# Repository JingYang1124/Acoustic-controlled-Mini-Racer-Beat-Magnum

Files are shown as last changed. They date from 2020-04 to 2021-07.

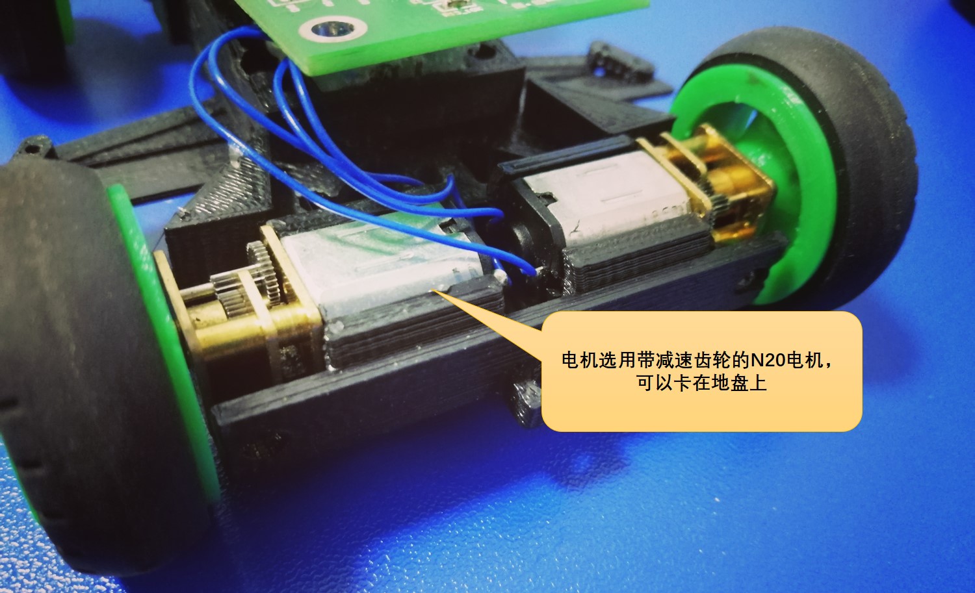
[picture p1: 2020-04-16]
Image/2_电机固定.jpg

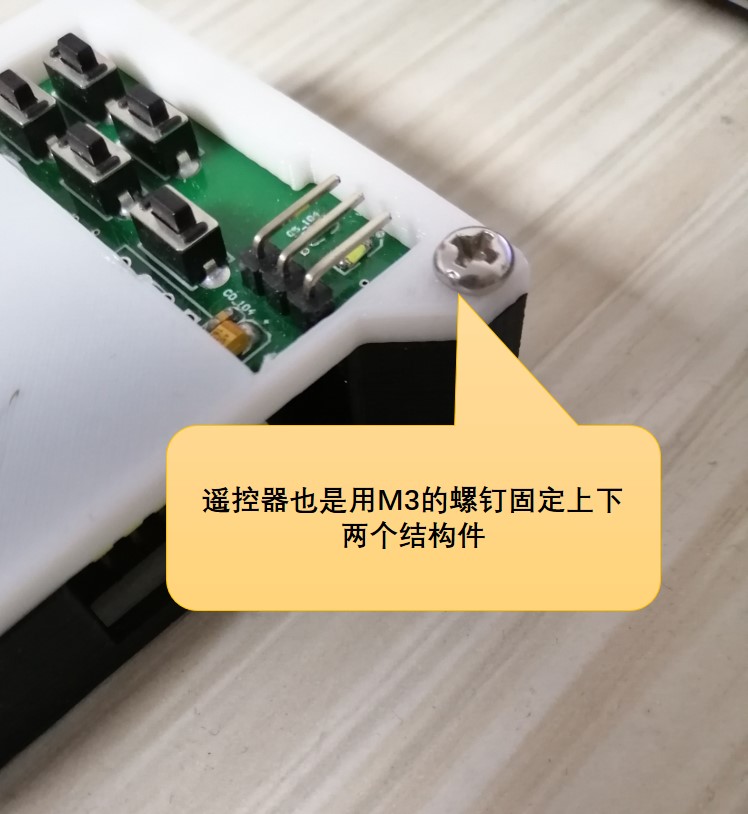
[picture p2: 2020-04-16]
Image/6_遥控器固定.jpg

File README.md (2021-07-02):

# 声控的迷你赛车--“跃动冲锋”
  

本项目是一款声控的迷你赛车--“跃动冲锋”，可通过语音指令控制车子的运动，还原了动画片“四驱兄弟”中的场景。

项目演示视频：

> [【自制】声控版! 前进，跃动冲锋！_哔哩哔哩_bilibili](https://www.bilibili.com/video/BV11g4y1879b)

1_声控版“跃动冲锋”

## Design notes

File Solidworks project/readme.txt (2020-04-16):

Solidworks版本：Solidworks 18   
Car_base文件夹中工程为车子底盘的模型
Transmitter文件夹中工程为遥控器的模型

上述文件夹内包括了装配体模型以及每一个小部件的模型

如果您的Solidworks版本低打不开上述模型，或者没有您安装solidworks，也可以直接使用stl文件进行3D打印
底盘打印时，可以直接打印：
mark3.STL                （1个）
back_lock.STL          （1个）
back_wheel.STL       （2个）
Racer_Lock.STL        （1个）
board_support.STL  （1个）
frontwheellock.STL  （2个）

遥控器打印时，可以直接打印：
Transmitter_base.STL    （1个）
Trans_part2.STL            （1个）

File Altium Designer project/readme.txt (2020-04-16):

Altium Designer版本：Altium Designer 18   
Beat_magnum_transmitter 文件夹中工程为语音遥控器的PCB
Beat_magnum_receiver 文件夹中工程为车子上的PCB

文件夹内包含了PCB导出的Gerber文件，可以直接将其发送给PCB厂家生产

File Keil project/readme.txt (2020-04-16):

Keil版本： Keil 5
Beat_magnum_transmitter 为语音遥控器上的程序
Beat_magnum_receiver 为车子上的程序

在两个工程中，将关于端口以及语音指令信息汇总在USER_HARDWARE_CONFIG.c以及USER_HARDWARE_CONFIG.h中，
您可以通过这两个文件快捷地对端口以及语音指令信息进行修改。

关于LD3320语音芯片的使用，可以参阅网站： http://www.icroute.com/  中的芯片开发手册

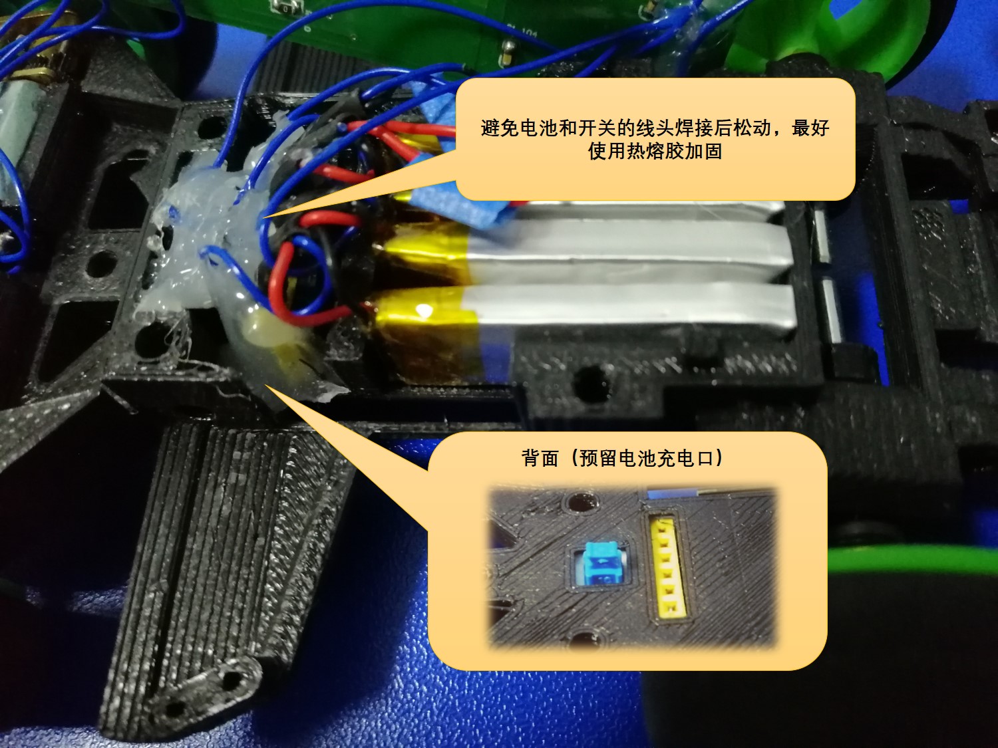
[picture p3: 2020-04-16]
Image/3_电池和开关的固定.jpg

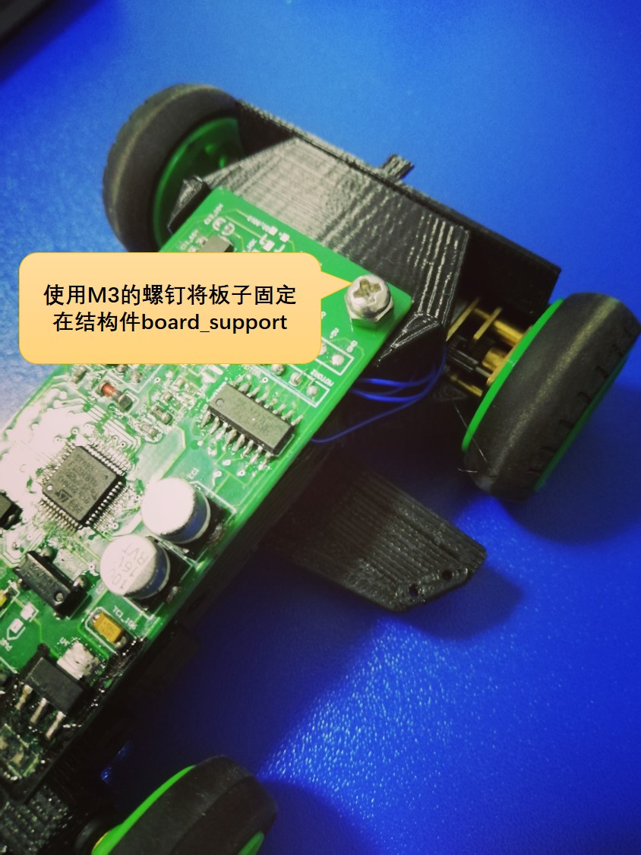
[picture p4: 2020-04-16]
Image/5_电路板固定.jpg

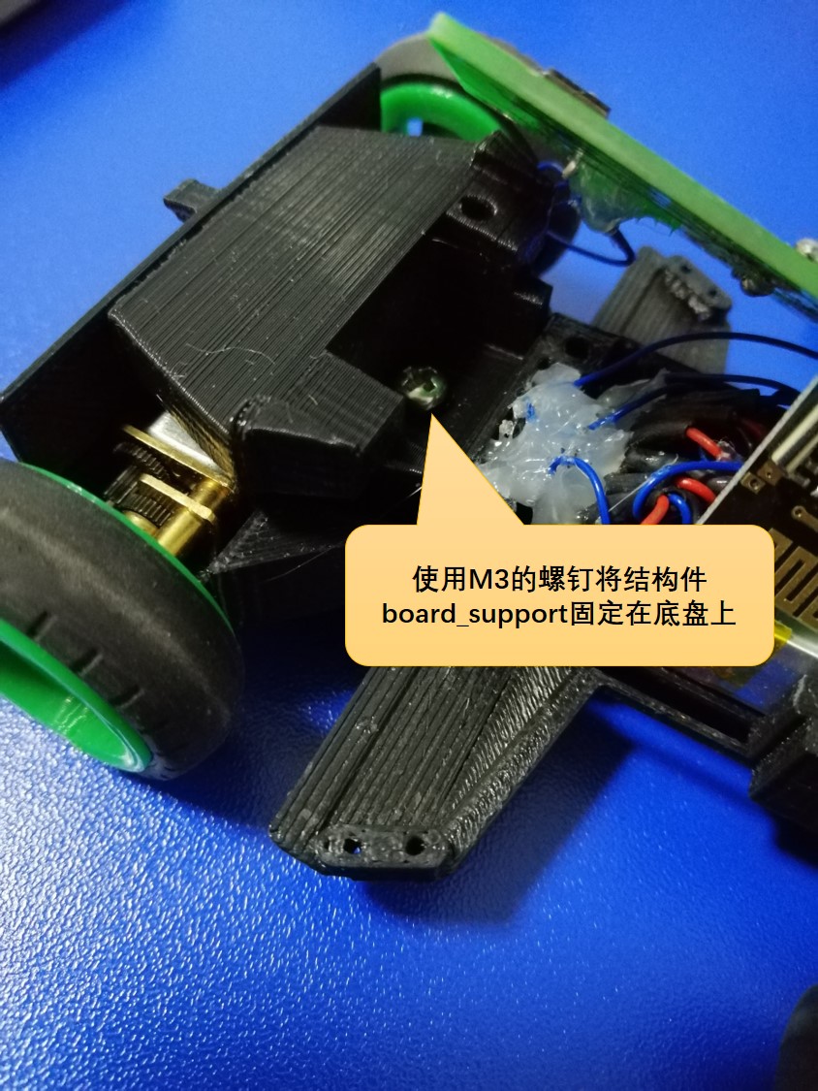
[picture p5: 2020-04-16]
Image/4_board_support的固定.jpg

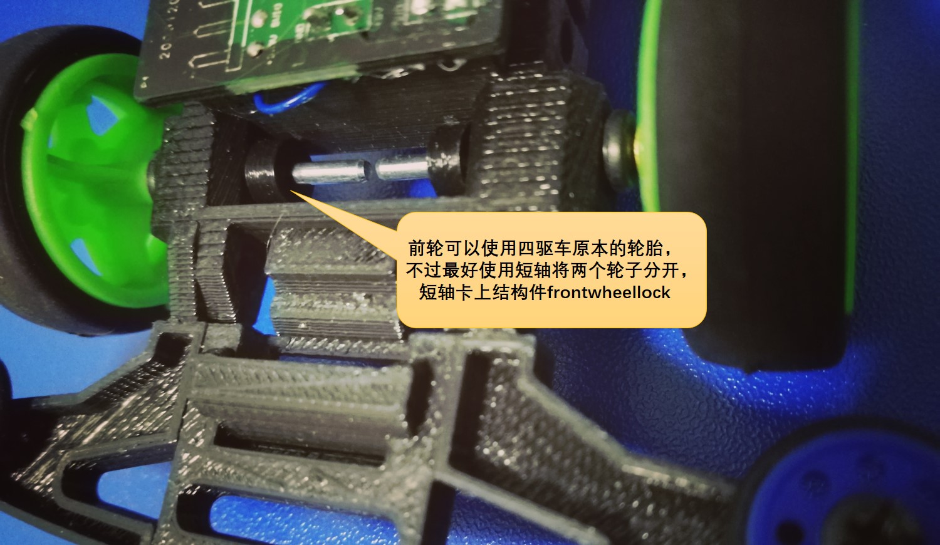
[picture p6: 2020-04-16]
Image/1_前轮固定.jpg

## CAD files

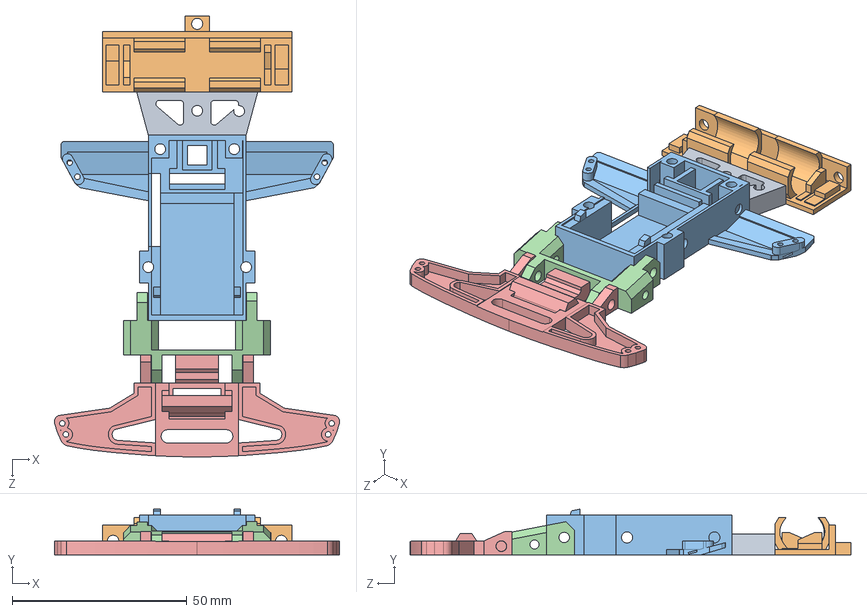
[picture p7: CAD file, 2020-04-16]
Solidworks project/Car_Base/mark3.SLDASM
81.7 x 13.1 x 126.3 mm
chip
电机支撑
battery
frontwheel
lead

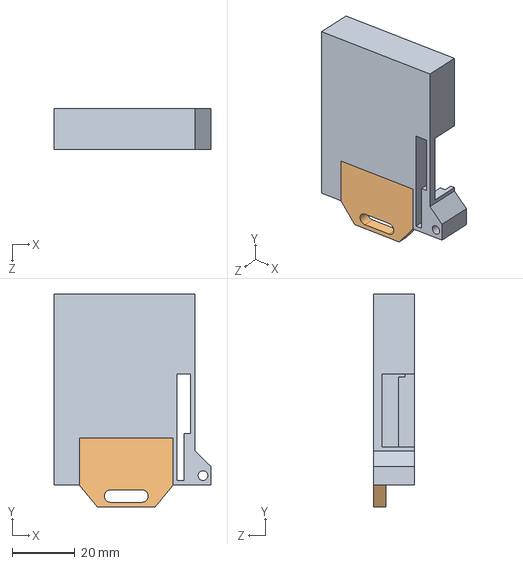
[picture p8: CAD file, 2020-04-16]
Solidworks project/Transmitter/Transmitter_base.SLDASM
50.0 x 68.0 x 13.0 mm
Trans_part1
Hang_Hole

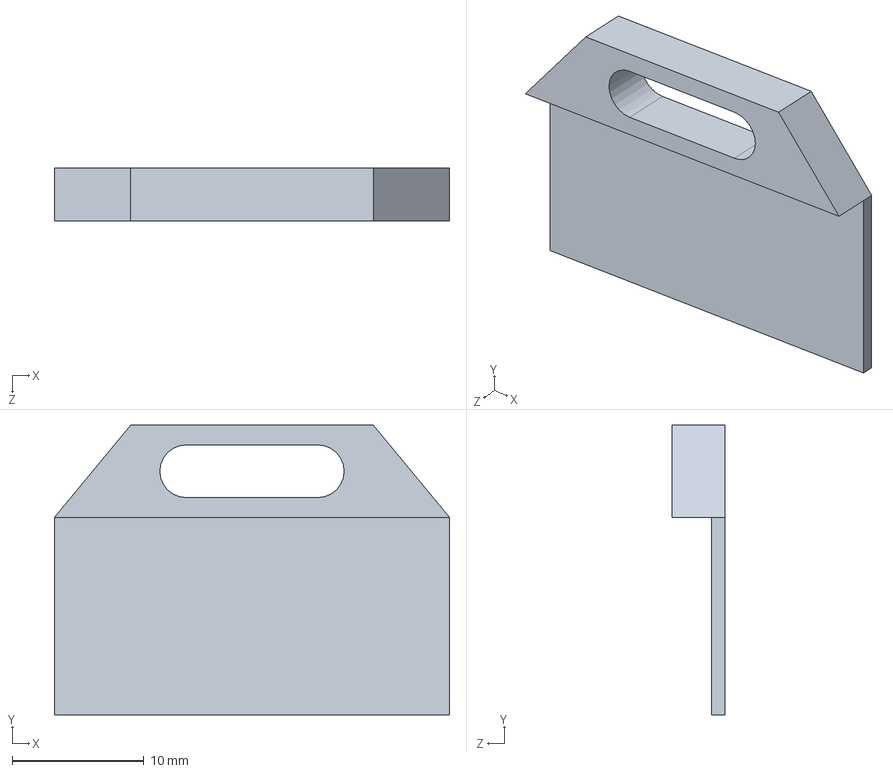
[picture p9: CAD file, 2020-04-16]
Solidworks project/Transmitter/Hang_Hole.SLDPRT
30.0 x 22.0 x 4.00 mm

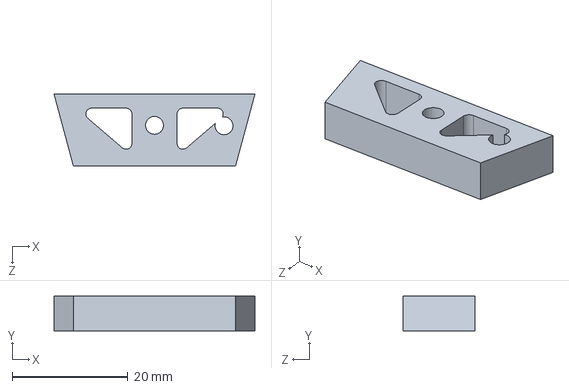
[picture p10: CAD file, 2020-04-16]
Solidworks project/Car_Base/chip.SLDPRT
34.7 x 6.00 x 12.4 mm

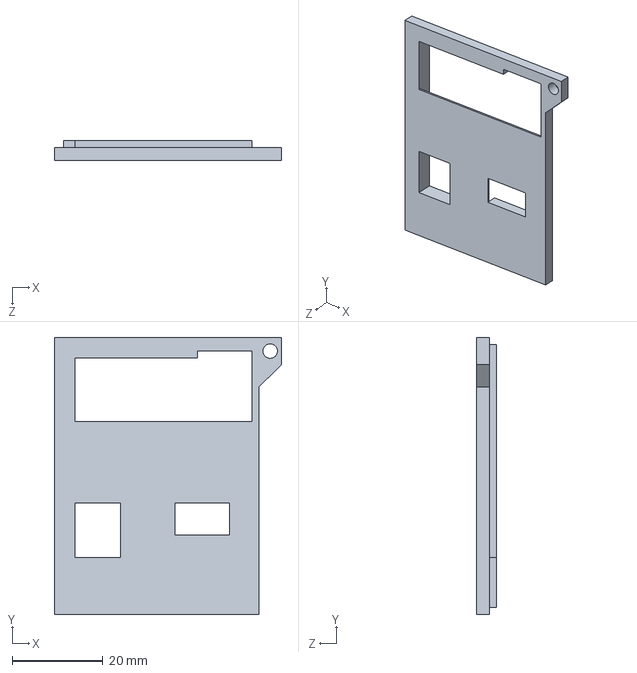
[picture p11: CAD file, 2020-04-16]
Solidworks project/Transmitter/Trans_part2.SLDPRT
50.0 x 61.0 x 4.30 mm

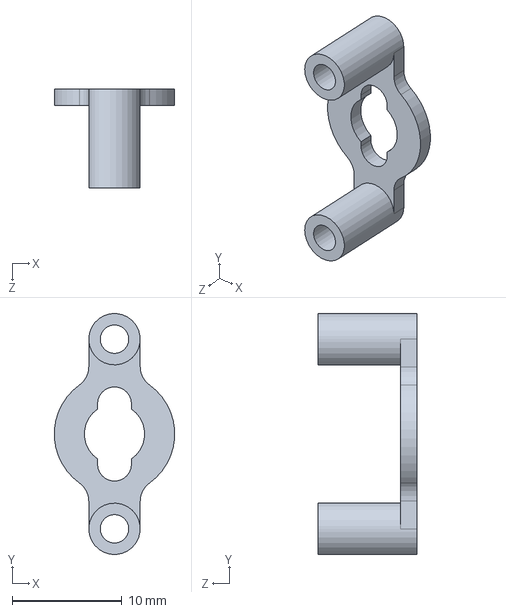
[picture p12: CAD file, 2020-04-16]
Solidworks project/Car_Base/Racer_Lock.SLDPRT
11.0 x 22.0 x 9.00 mm

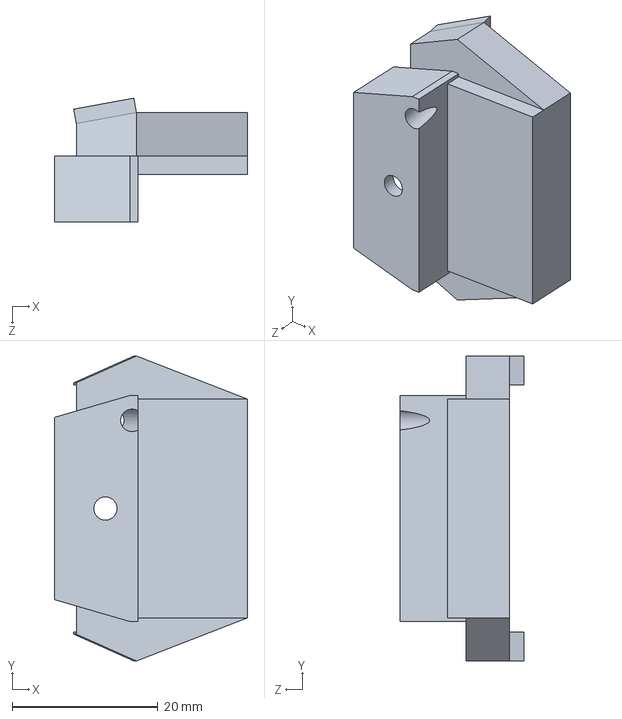
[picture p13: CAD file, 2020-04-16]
Solidworks project/Car_Base/board_support.SLDPRT
26.5 x 41.8 x 17.0 mm

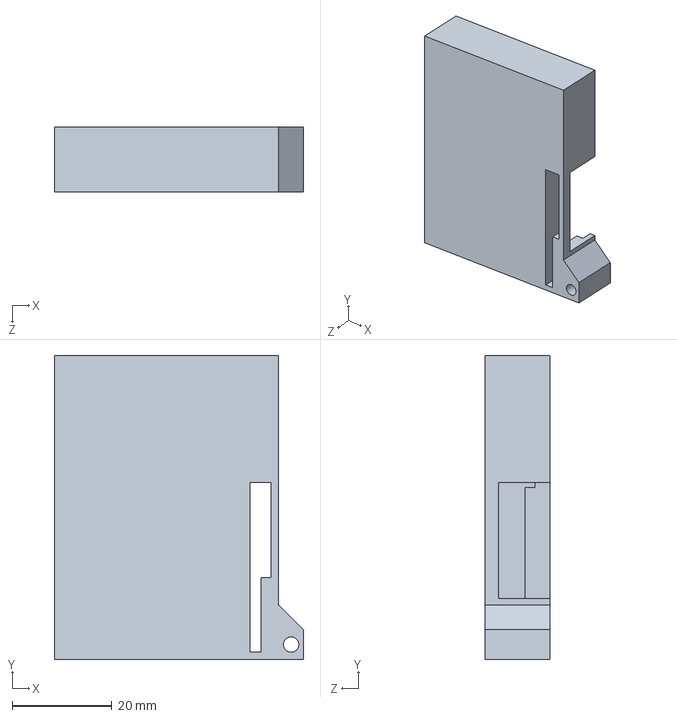
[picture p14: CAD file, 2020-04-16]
Solidworks project/Transmitter/Trans_part1.SLDPRT
50.0 x 61.0 x 13.0 mm

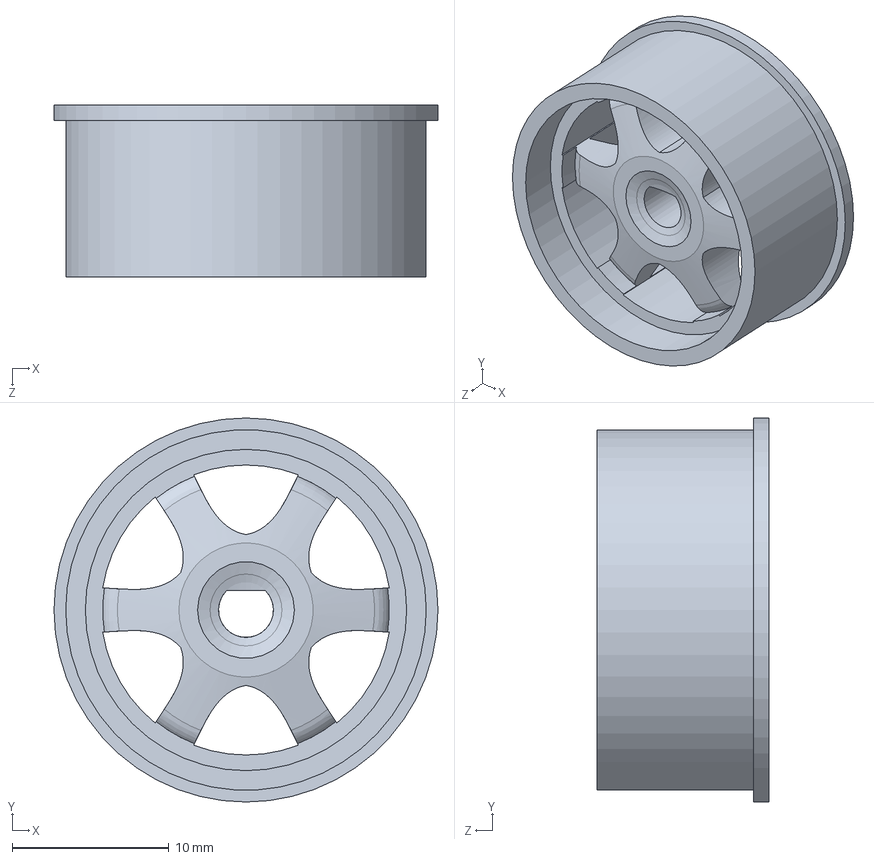
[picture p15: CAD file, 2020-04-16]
Solidworks project/Car_Base/back_wheel.SLDPRT
24.5 x 24.5 x 11.0 mm

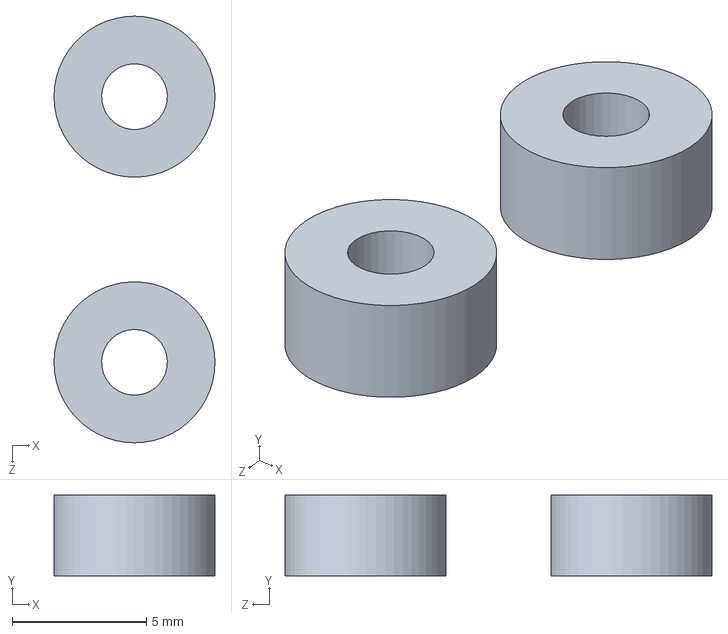
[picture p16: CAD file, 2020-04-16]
Solidworks project/Car_Base/frontwheellock.SLDPRT
6.00 x 3.00 x 15.9 mm

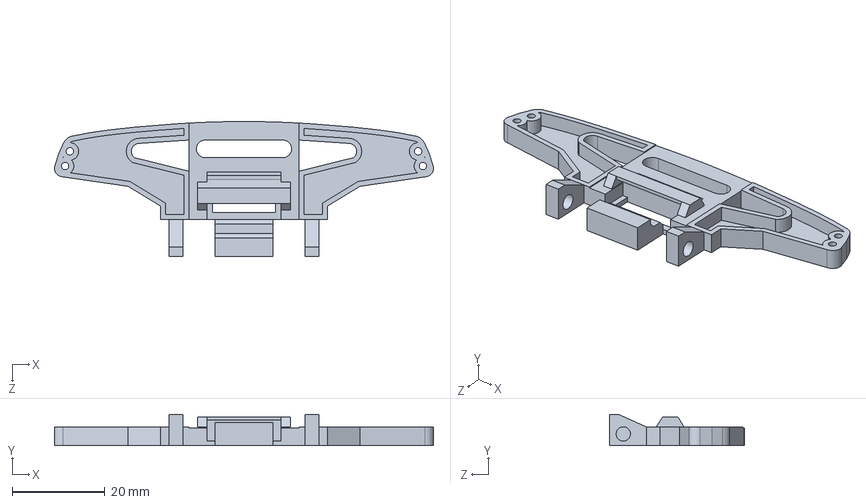
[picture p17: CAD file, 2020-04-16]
Solidworks project/Car_Base/lead.SLDPRT
81.7 x 6.70 x 29.2 mm

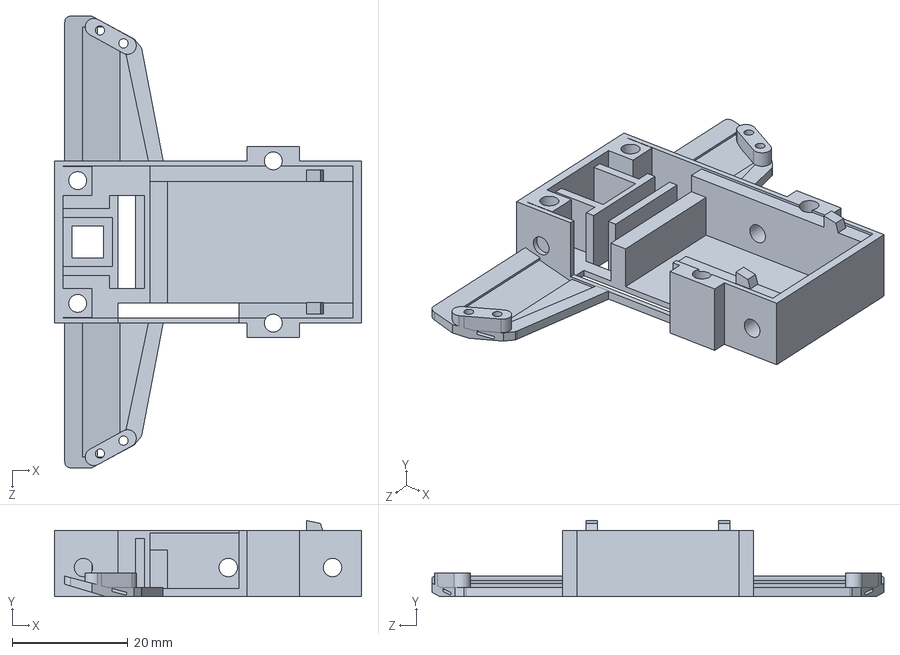
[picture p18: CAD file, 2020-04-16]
Solidworks project/Car_Base/battery.SLDPRT
53.0 x 13.1 x 78.0 mm

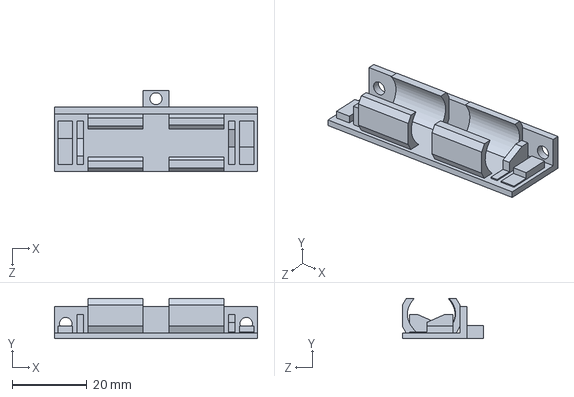
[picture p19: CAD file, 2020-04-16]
Solidworks project/Car_Base/电机支撑.SLDPRT
54.2 x 10.7 x 21.7 mm

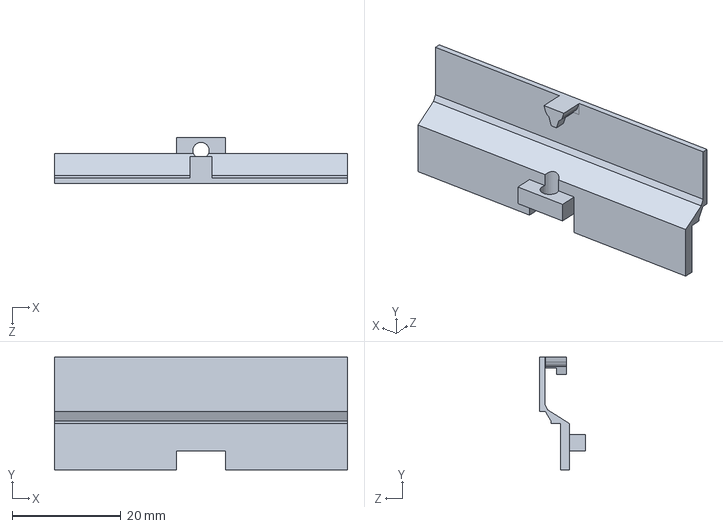
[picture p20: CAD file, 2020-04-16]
Solidworks project/Car_Base/back_lock.SLDPRT
54.0 x 20.8 x 8.50 mm

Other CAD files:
Solidworks project/Car_Base/frontwheel.SLDPRT
Solidworks project/Car_Base/Racer_Lock.STL
Solidworks project/Car_Base/back_lock.STL
Solidworks project/Car_Base/back_wheel.STL
Solidworks project/Car_Base/battery.STL
Solidworks project/Car_Base/board_support.STL
Solidworks project/Car_Base/chip.STL
Solidworks project/Car_Base/frontwheel.STL
Solidworks project/Car_Base/frontwheellock.STL
Solidworks project/Car_Base/lead.STL
Solidworks project/Car_Base/mark3.STL
Solidworks project/Car_Base/电机支撑.STL
Solidworks project/Transmitter/Hang_Hole.STL
Solidworks project/Transmitter/Trans_part1.STL
Solidworks project/Transmitter/Trans_part2.STL
Solidworks project/Transmitter/Transmitter_base.STL

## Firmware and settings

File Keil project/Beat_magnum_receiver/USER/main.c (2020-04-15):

#include "led.h"
#include "delay.h"
#include "sys.h"
#include "timer.h"
#include "24l01.h"
#include "MX1508.h"
#include "USER_HARDWARE_CONFIG.h"

#define RC_STOP  0
#define RC_RUN_F 1
#define RC_RUN_B 2


char RunState = RC_STOP;
	
char INA1_PWM = 0;//Right wheel go backward
char INB1_PWM = 0;//Right wheel go forward
char INA2_PWM = 0;//Left wheel go forward
char INB2_PWM = 0;//Left wheel go backward

	u16 t=0;	
	u8 tmp_buf[33];		
	u8  Send_State;

	float HCSR_Value;

 int main(void)
 {
	u8 silentcount = 0;
 
	delay_init();	    	 //延时函数初始化	  
	NVIC_PriorityGroupConfig(NVIC_PriorityGroup_2); 	 //设置NVIC中断分组2:2位抢占优先级，2位响应优先级
	LED_Init();
	MX1508_Init();
	TIM2_Int_Init(5,7200);    // New time base: 72M / 7200 = 10000Hz; Every inttrupt time gap: 1/10000Hz * 5 = 0.5ms  	   	 

	NRF24L01_Init();    		//初始化NRF24L01 
	LED0 = 0;
	NRF24L01_RX_Mode();		  
			
	for(t=0;t<32;t++)
	{
		tmp_buf[t]='A';	
	}	  
	tmp_buf[32]=0;//加入结束符		 
	while(1)
	{			
		
		if(NRF24L01_RxPacket(tmp_buf)==0)//一旦接收到信息,则显示出来.
			{
				silentcount = 0;
				tmp_buf[32]=0;//加入字符串结束符
				if(tmp_buf[0] == NRF_COMMAND_YDCF) //“跃动冲锋” 亮灯
				{
					LED0=!LED0;
				}
				if(tmp_buf[0] == NRF_COMMAND_T)    //“停”
				{
					RunState = RC_STOP;
					INA1_PWM = 0;
					INB1_PWM = 0;
					INA2_PWM = 0;
					INB2_PWM = 0;
				}
				if(tmp_buf[0] == NRF_COMMAND_QJ)   //“前进”
				{
					if(RunState == RC_STOP || RunState == RC_RUN_F)
					{
						INA1_PWM = 0;
						INB1_PWM = 70;
						INA2_PWM = 70;
						INB2_PWM = 0;
						RunState = RC_RUN_F;
					}
				}
				if(tmp_buf[0] == NRF_COMMAND_JS)   //“加速”
				{
					if(RunState == RC_STOP || RunState == RC_RUN_F)
					{
						INA1_PWM = 0;
						INB1_PWM = 95;
						INA2_PWM = 95;
						INB2_PWM = 0;
						RunState = RC_RUN_F;
					}
				}
				if(tmp_buf[0] == NRF_COMMAND_HT)   //“后退”
				{
					if(RunState == RC_STOP)
					{
						INA1_PWM = 70;
						INB1_PWM = 0;
						INA2_PWM = 0;
						INB2_PWM = 70;
						RunState = RC_RUN_B;
					}
				}
				if(tmp_buf[0] == NRF_COMMAND_XZ)   //“向左”
				{
					if(RunState == RC_STOP || RunState == RC_RUN_F)
					{
						INA1_PWM = 0;
						INB1_PWM = 80;
						INA2_PWM = 45;
						INB2_PWM = 0;
						RunState = RC_RUN_F;
					}
				}
				if(tmp_buf[0] == NRF_COMMAND_XY)   //“向右”
				{
					if(RunState == RC_STOP || RunState == RC_RUN_F)
					{
						INA1_PWM = 0;
						INB1_PWM = 45;
						INA2_PWM = 80;
						INB2_PWM = 0;
						RunState = RC_RUN_F;
					}
				}
			}
			else
			{
					silentcount ++;
					if(silentcount == 20)  //连续20次循环没有接收到遥控信息，则自动停止
					{
						RunState = RC_STOP;
						INA1_PWM = 0;
						INB1_PWM = 0;
						INA2_PWM = 0;
						INB2_PWM = 0;
						silentcount = 0;
					}
					delay_ms(10);	  
			}
	}	 
 }

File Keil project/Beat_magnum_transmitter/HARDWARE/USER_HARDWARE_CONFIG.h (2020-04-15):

#ifndef USER_HARDWARE_CONFIG_H
#define USER_HARDWARE_CONFIG_H 	

#include "sys.h"

/*************LD3320 端口信息********************
 * RST      PA3
 * CS   	  PA2
 * WR/SPIS  PA0
 * P2/SDCK  PA5
 * P1/SDO   PA6
 * P0/SDI   PA7
 * IRQ      PB1
 * A0				PA4
*****************************************/
/********************NRF24L01信息********************
 * NRF24L01_IRQ         PB6
 * NRF24L01_CSN      	  PB7
 * NRF24L01_CE          PB8
 * NRF24L01_SCK         PB13
 * NRF24L01_MISO        PB14
 * NRF24L01_MOSI        PB15
*****************************************/
/********************按键信息********************
 * KEY_UP(前进)         PA8
 * KEY_DOWN(后退)   	  PA11
 * KEY_LEFT(向左)       PA12
 * KEY_RIGHT(向右)      PA15
 * KEY_STOP(停止)       PB9
*****************************************/

#define PORT_LD_SPI         GPIOA //LD的MOSI\MISO\SCK都在GPIOA上
#define PORT_LD_CE          GPIOA
#define PORT_LD_RST         GPIOA
#define PORT_LD_A0          GPIOA
#define PORT_LD_SPIS        GPIOA
#define PORT_LD_IRQ         GPIOB

#define PIN_LD_SPI_SCK      GPIO_Pin_5
#define PIN_LD_SPI_MISO     GPIO_Pin_6
#define PIN_LD_SPI_MOSI     GPIO_Pin_7
#define PIN_LD_CE           GPIO_Pin_2
#define PIN_LD_RST          GPIO_Pin_3
#define PIN_LD_A0           GPIO_Pin_4
#define PIN_LD_SPIS         GPIO_Pin_0
#define PIN_LD_IRQ          GPIO_Pin_1

#define PORT_NRF24L01       GPIOB
#define PIN_NRF24L01_IRQ    GPIO_Pin_6
#define PIN_NRF24L01_CSN    GPIO_Pin_7
#define PIN_NRF24L01_CE     GPIO_Pin_8
#define PIN_NRF24L01_SCK    GPIO_Pin_13
#define PIN_NRF24L01_MISO   GPIO_Pin_14
#define PIN_NRF24L01_MOSI   GPIO_Pin_15


#define PORT_KEY_MOVE       GPIOA
#define PORT_KEY_STOP       GPIOB
#define PIN_KEY_UP          GPIO_Pin_8
#define PIN_KEY_DOWN        GPIO_Pin_11
#define PIN_KEY_LEFT        GPIO_Pin_12
#define PIN_KEY_RIGHT       GPIO_Pin_15
#define PIN_KEY_STOP        GPIO_Pin_9


#define DATE_A           7     /*识别短语数量*/
#define DATE_B           20		/*单个短语的拼音总长度上限(最大79)*/

//用来对pCode数组进行赋值，有几个短语就需要进行几个宏定义，后面的数字可以自定义，但是建议如下依次增加
#define CODE_YDCF	       1	 /*跃动冲锋*/
#define CODE_QJ	         2	 /*前进*/
#define CODE_T	         3	 /*停*/
#define CODE_HT	         4	 /*后退*/
#define CODE_JS          5   /*加速*/
#define CODE_XZ          6   /*向左*/
#define CODE_XY          7   /*向右*/

#define CLK_IN           8	 /* LD3320使用的晶振频率（单位：Mhz）*/
#define MIC_VOL          0x10 //可以设置 00H-7FH，越小需要距离越近才能识别，对于远处的干扰具有一定的抵抗能力
#define Vad_Silence_End  0x0A //设置LD3320的B5寄存器，每一单位代表10毫秒。表示检测到语音段后连续检测这么长时间的噪声认为是语音结束
#define Vad_Length       0xA  //设置LD3320的B6寄存器，每一单位代表100毫秒。代表检测到语音段后最长允许多久的语音识别

//以下为NRF24L01发送的数据
#define NRF_COMMAND_YDCF  'Y'
#define NRF_COMMAND_QJ    'Q'
#define NRF_COMMAND_T     'T'
#define NRF_COMMAND_HT    'H'
#define NRF_COMMAND_JS    'J'
#define NRF_COMMAND_XZ    'L'
#define NRF_COMMAND_XY    'R' 

//NRF24L01操作线
#define NRF24L01_CE   PBout(8) //24L01片选信号
#define NRF24L01_CSN  PBout(7) //SPI片选信号	   
#define NRF24L01_IRQ  PBin(6)  //IRQ主机数据输入


//*****************************************************************
//*****************************************************************
//以下内容可以不用修改，下面的宏定义依赖于上面内容//
//*****************************************************************
//*****************************************************************
#define KEY_UP      GPIO_ReadInputDataBit(PORT_KEY_MOVE,PIN_KEY_UP)
#define KEY_DOWN    GPIO_ReadInputDataBit(PORT_KEY_MOVE,PIN_KEY_DOWN)
#define KEY_LEFT    GPIO_ReadInputDataBit(PORT_KEY_MOVE,PIN_KEY_LEFT)
#define KEY_RIGHT   GPIO_ReadInputDataBit(PORT_KEY_MOVE,PIN_KEY_RIGHT) 
#define KEY_STOP    GPIO_ReadInputDataBit(PORT_KEY_STOP,PIN_KEY_STOP) 

#define LD_RST_H() GPIO_SetBits(PORT_LD_RST, PIN_LD_RST )
#define LD_RST_L() GPIO_ResetBits(PORT_LD_RST, PIN_LD_RST )

#define LD_CS_H()	GPIO_SetBits(PORT_LD_CE, PIN_LD_CE)
#define LD_CS_L()	GPIO_ResetBits(PORT_LD_CE, PIN_LD_CE)

#define LD_MOSI_H()	GPIO_SetBits(PORT_LD_SPI, PIN_LD_SPI_MOSI)
#define LD_MOSI_L()	GPIO_ResetBits(PORT_LD_SPI, PIN_LD_SPI_MOSI)

#define LD_SCK_H()	GPIO_SetBits(PORT_LD_SPI, PIN_LD_SPI_SCK)
#define LD_SCK_L()	GPIO_ResetBits(PORT_LD_SPI, PIN_LD_SPI_SCK)

#define LD_SPIS_H()  GPIO_SetBits(PORT_LD_SPIS, PIN_LD_SPIS)
#define LD_SPIS_L()  GPIO_ResetBits(PORT_LD_SPIS, PIN_LD_SPIS)

#define LD_MISO      GPIO_ReadInputDataBit(PORT_LD_SPI,PIN_LD_SPI_MISO)

extern u8  sRecog[DATE_A][DATE_B];
extern u8  pCode[DATE_A];
//*****************************************************************
//*****************************************************************

#endif

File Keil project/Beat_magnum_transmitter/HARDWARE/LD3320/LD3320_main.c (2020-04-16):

#include    <stm32f10x.h>
#include "stm32f10x_conf.h"
#include "LDchip.h"
#include "Reg_RW.h"
#include "USER_HARDWARE_CONFIG.h"
#include "24l01.h" 	 


extern u8  tmp_buf[33];	
extern u8  Send_State;


/************************************************************************************
//	nAsrStatus 用来在main主程序中表示程序运行的状态，不是LD3320芯片内部的状态寄存器
//	LD_ASR_NONE:		表示没有在作ASR识别
//	LD_ASR_RUNING：		表示LD3320正在作ASR识别中
//	LD_ASR_FOUNDOK:		表示一次识别流程结束后，有一个识别结果
//	LD_ASR_FOUNDZERO:	表示一次识别流程结束后，没有识别结果
//	LD_ASR_ERROR:		表示一次识别流程中LD3320芯片内部出现不正确的状态
*********************************************************************************/
u8 nAsrStatus = LD_ASR_NONE;	

void LD3320_Init(void);

u8 RunASR(void);
void ProcessInt0(void);
void LD3320_EXTI_Cfg(void);
void LD3320_Spi_cfg(void);
void LD3320_GPIO_Cfg(void);

/***********************************************************
* 名    称： LD3320_main(void)
* 功    能： 主函数LD3320程序入口
**********************************************************/ 

void  LD3320_main(void)
{
	u8 Ori_tmp;
	u8 nAsrRes=0;
 	switch(nAsrStatus)
		{
			case LD_ASR_RUNING:
												break;
			case LD_ASR_ERROR:		
											tmp_buf[0]='D';	
												break;
			case LD_ASR_NONE:
											nAsrStatus=LD_ASR_RUNING;
											if (RunASR()==0)	//	启动一次ASR识别流程：ASR初始化，ASR添加关键词语，启动ASR运算
											{		
												nAsrStatus = LD_ASR_ERROR;
											}
											break;

			case LD_ASR_FOUNDOK:
											 nAsrRes = LD_GetResult( );	//	一次ASR识别流程结束，去取ASR识别结果	
												 switch(nAsrRes)		   
												  {
													  case CODE_YDCF:			/*Beat magnum*/
														Ori_tmp = tmp_buf[0];
														tmp_buf[0] = NRF_COMMAND_YDCF;
														Send_State = NRF24L01_TxPacket(tmp_buf);
														tmp_buf[0] = Ori_tmp;
																						 break;
														case CODE_QJ:	      /*Go forward*/
														tmp_buf[0] = NRF_COMMAND_QJ;															
																						 break;
														case CODE_T:		    /*Stop*/
														tmp_buf[0] = NRF_COMMAND_T;															
																						break;
														case CODE_HT:		    /*Go backward*/
														tmp_buf[0] = NRF_COMMAND_HT;																								
																						break;
														case CODE_JS:       /*Accelerate*/
														tmp_buf[0] = NRF_COMMAND_JS;																								
																						break;
														case CODE_XZ:       /*Turn left*/
														tmp_buf[0] = NRF_COMMAND_XZ;																								
																						break;
														case CODE_XY:       /*Turn rught*/
														tmp_buf[0] = NRF_COMMAND_XY;																							
																						break;
														default:break;
													}

												nAsrStatus = LD_ASR_NONE;
											break;
			case LD_ASR_FOUNDZERO:
			default:
								nAsrStatus = LD_ASR_NONE;
								break;
			}

}
/***********************************************************
* 名    称：LD3320_Init(void)
* 功    能：模块驱动端口初始配置
**********************************************************/ 
void LD3320_Init(void)
{
	LD3320_GPIO_Cfg();	
	LD3320_EXTI_Cfg();
	LD3320_Spi_cfg();	 

	LD_reset();
}

/***********************************************************
* 名    称：	LD3320_delay(unsigned long uldata)
* 功    能：	非精确延时
**********************************************************/ 
void Delay_( int i)
 {     
    while( i--)
       {	

        }
 }	

 void  LD3320_delay(unsigned long uldata)
{
	unsigned int j  =  0;
	unsigned int g  =  0;
	for (j=0;j<5;j++)
	{
		for (g=0;g<uldata;g++)
		{
			Delay_(10);
		}
	}
}

/***********************************************************
* 名    称：	RunASR(void)
* 功    能：	运行ASR
**********************************************************/ 
u8 RunASR(void)
{
	u8 i=0;
	u8 asrflag=0;
	for (i=0; i<5; i++)			//	防止由于硬件原因导致LD3320芯片工作不正常，所以一共尝试5次启动ASR识别流程
	{
		LD_AsrStart();			//初始化ASR
		LD3320_delay(20);
		if (LD_AsrAddFixed()==0)	
		{
			LD_reset();			
			LD3320_delay(20);			
			continue;
		}

		LD3320_delay(10);

		if (LD_AsrRun() == 0)
		{
			LD_reset();			
			LD3320_delay(20);			
			continue;
		}

		asrflag=1;
		break;					
	}

	return asrflag;
}


void LD3320_GPIO_Cfg(void)
{	
	 GPIO_InitTypeDef GPIO_InitStructure;
	   //io口配置
		//LD_CS	/LD_RST /LD_A0
	  RCC_APB2PeriphClockCmd(RCC_APB2Periph_GPIOA | RCC_APB2Periph_AFIO, ENABLE);
		GPIO_InitStructure.GPIO_Pin =PIN_LD_CE|PIN_LD_RST|PIN_LD_A0;
		GPIO_InitStructure.GPIO_Speed = GPIO_Speed_50MHz;
		GPIO_InitStructure.GPIO_Mode = GPIO_Mode_Out_PP;
		GPIO_Init(GPIOA,&GPIO_InitStructure);

		GPIO_SetBits(PORT_LD_A0,PIN_LD_A0);	/*A0默认拉高*/
}
/***********************************************************
* 名    称：LD3320_Spi_cfg(void)
* 功    能：配置SPI功能和端口初始化
**********************************************************/ 
void LD3320_Spi_cfg(void)
{
	GPIO_InitTypeDef GPIO_InitStructure;

	RCC_APB1PeriphClockCmd(RCC_APB2Periph_GPIOA,ENABLE);	   
  
	GPIO_InitStructure.GPIO_Pin = PIN_LD_SPIS;			
	GPIO_InitStructure.GPIO_Speed = GPIO_Speed_50MHz;
	GPIO_InitStructure.GPIO_Mode = GPIO_Mode_Out_PP;
	GPIO_Init(PORT_LD_SPIS, &GPIO_InitStructure);
  
	//P0/P1/P2 用来进行SPI通信,且使用软件模拟SPI通信
	GPIO_InitStructure.GPIO_Pin = PIN_LD_SPI_SCK | PIN_LD_SPI_MOSI;
	GPIO_InitStructure.GPIO_Speed = GPIO_Speed_50MHz;
	GPIO_InitStructure.GPIO_Mode = GPIO_Mode_Out_PP;
	GPIO_Init(PORT_LD_SPI,&GPIO_InitStructure);

	GPIO_InitStructure.GPIO_Pin = PIN_LD_SPI_MISO;
	GPIO_InitStructure.GPIO_Mode = GPIO_Mode_IN_FLOATING;
	GPIO_Init(PORT_LD_SPI,&GPIO_InitStructure);
	
	LD_CS_H();
	LD_MOSI_H();
	LD_SCK_H();
}
/***********************************************************
* 名    称： LD3320_EXTI_Cfg(void) 
* 功    能： 外部中断功能配置和相关端口配置
**********************************************************/ 
void LD3320_EXTI_Cfg(void)
{
  EXTI_InitTypeDef EXTI_InitStructure;
	NVIC_InitTypeDef NVIC_InitStructure;
  GPIO_InitTypeDef GPIO_InitStructure;

  //中断引脚配置
  RCC_APB2PeriphClockCmd(RCC_APB2Periph_GPIOB, ENABLE);
  GPIO_InitStructure.GPIO_Pin = PIN_LD_IRQ;
  GPIO_InitStructure.GPIO_Mode = GPIO_Mode_IN_FLOATING;
  GPIO_InitStructure.GPIO_Speed = GPIO_Speed_50MHz;
  GPIO_Init(PORT_LD_IRQ, &GPIO_InitStructure);
	//外部中断线配置
  GPIO_EXTILineConfig(GPIO_PortSourceGPIOB, GPIO_PinSource1);
  EXTI_InitStructure.EXTI_Line = EXTI_Line1;
  EXTI_InitStructure.EXTI_Mode = EXTI_Mode_Interrupt;
  EXTI_InitStructure.EXTI_Trigger =EXTI_Trigger_Falling;
  EXTI_InitStructure.EXTI_LineCmd = ENABLE;
  EXTI_Init(&EXTI_InitStructure);
  EXTI_GenerateSWInterrupt(EXTI_Line1);
		
	GPIO_SetBits(PORT_LD_IRQ,PIN_LD_IRQ);	 //默认拉高中断引脚

	EXTI_ClearFlag(EXTI_Line1);
	EXTI_ClearITPendingBit(EXTI_Line1);
	//中断嵌套配置
  NVIC_InitStructure.NVIC_IRQChannel = EXTI1_IRQn;
  NVIC_InitStructure.NVIC_IRQChannelPreemptionPriority = 0;
  NVIC_InitStructure.NVIC_IRQChannelSubPriority = 0;
  NVIC_InitStructure.NVIC_IRQChannelCmd = ENABLE;
  NVIC_Init(&NVIC_InitStructure);
}
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

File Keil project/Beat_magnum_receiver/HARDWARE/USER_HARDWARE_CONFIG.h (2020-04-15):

#ifndef USER_HARDWARE_CONFIG_H
#define USER_HARDWARE_CONFIG_H 	

/********************NRF24L01信息********************
 * NRF24L01_IRQ         PB6
 * NRF24L01_CSN      	  PB7
 * NRF24L01_CE          PB8
 * NRF24L01_SCK         PB13
 * NRF24L01_MISO        PB14
 * NRF24L01_MOSI        PB15
*****************************************/
/********************MX1508信息********************
 * INA1                 PA1
 * INB1                 PA2
 * INA2                 PA3
 * INB2                 PA4
*****************************************/

#define PORT_NRF24L01       GPIOB
#define PIN_NRF24L01_IRQ    GPIO_Pin_6
#define PIN_NRF24L01_CSN    GPIO_Pin_7
#define PIN_NRF24L01_CE     GPIO_Pin_8
#define PIN_NRF24L01_SCK    GPIO_Pin_13
#define PIN_NRF24L01_MISO   GPIO_Pin_14
#define PIN_NRF24L01_MOSI   GPIO_Pin_15

#define PORT_MX1508         GPIOA
#define PIN_INA1            GPIO_Pin_1
#define PIN_INB1            GPIO_Pin_2
#define PIN_INA2            GPIO_Pin_3
#define PIN_INB2            GPIO_Pin_4

#define PORT_LED            GPIOC
#define PIN_LED             GPIO_Pin_13

//以下为NRF24L01发送的数据
#define NRF_COMMAND_YDCF  'Y'
#define NRF_COMMAND_QJ    'Q'
#define NRF_COMMAND_T     'T'
#define NRF_COMMAND_HT    'H'
#define NRF_COMMAND_JS    'J'
#define NRF_COMMAND_XZ    'L'
#define NRF_COMMAND_XY    'R' 

#define NRF24L01_CE   PBout(8) //24L01片选信号
#define NRF24L01_CSN  PBout(7) //SPI片选信号	   
#define NRF24L01_IRQ  PBin(6)  //IRQ主机数据输入


#define LED0 PCout(13)
#define INA1 PAout(1)	
#define INB1 PAout(2)	
#define INA2 PAout(3)	
#define INB2 PAout(4)	


//*****************************************************************
//*****************************************************************

#endif

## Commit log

2020-04-16 PCB files
    [MiniRacer_V2.GBL, MiniRacer_V2.GBO, MiniRacer_V2.GBP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]
2020-04-16 Solidworks project files
    [Hang_Hole.SLDPRT, Hang_Hole.STL, Racer_Lock.SLDPRT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]
